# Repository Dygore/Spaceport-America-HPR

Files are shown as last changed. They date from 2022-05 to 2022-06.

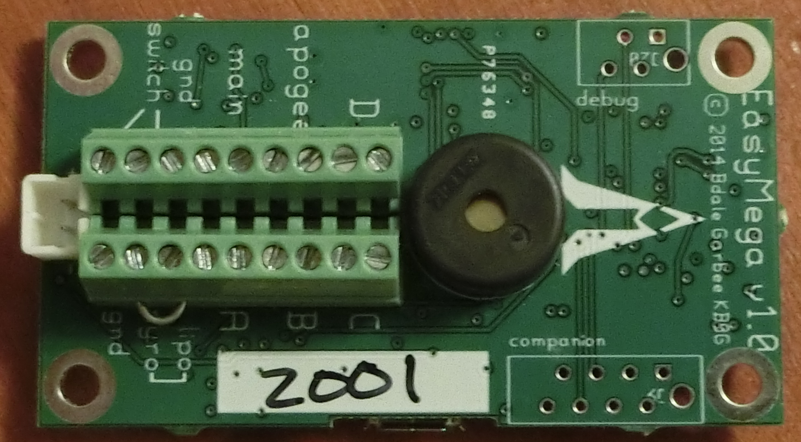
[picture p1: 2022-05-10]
altos/doc/easymega-v1.0-top.jpg

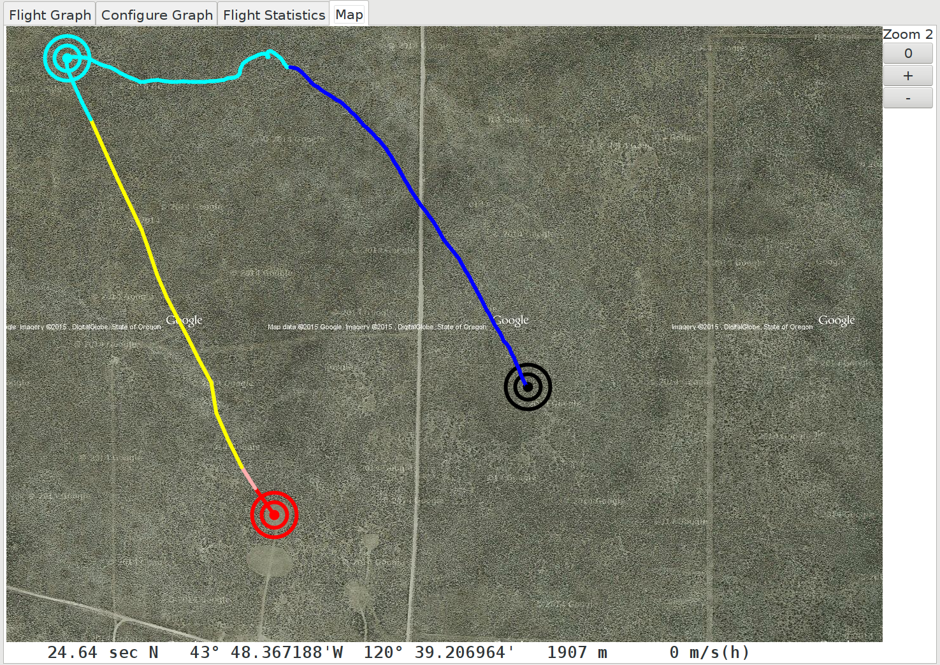
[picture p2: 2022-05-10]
altos/doc/graph-map.png

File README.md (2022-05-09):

# Oklahoma State University High Powered Rocketry Spaceport America



## About
This project will be used to create a working airbrake system for the Spaceport America Competition in June. The goal of this competition is to get as close to 10,000 feet as possible with a High Powered Rocket.

Our airbrake will be controlled by stepper motors with a gear increase for torque, which will turn a lead screw after the rocket motor has burnt out until apogee. The STM32 Board will receive telemetry data over SPI from the Telemega, it will access a lookup table on our flash chip to get the corresponding drag coefficients. It will then drive the stepper motor using a stepper motor controller to step the airbrake pads out, thus slowing down the rocket. This could be further enhanced using more accurate data and a PID controller.

## Details
The code will be written in two main sections
Section 1: STM32 code written in STM32 CubeIDE programmed using SWD pins
Section 2: Code written and built in Linux using Altus Metrum's Telemega code as a base

## References
For more information on the Altus Metrum Telemega visit https://altusmetrum.org/

Thank you to Bdale Garbee for his help in the development process and for designing the Telemega https://gag.com/bdale/

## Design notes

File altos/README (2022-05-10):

	AltOS - 8051 operating system for Altus-Metrum projects

Copyright and License

	Copyright © 2009 Keith Packard <keithp@keithp.com>

	This program is free software; you can redistribute it and/or modify
	it under the terms of the GNU General Public License as published by
	the Free Software Foundation; either version 2 of the License, or
	(at your option) any later version.

	This program is distributed in the hope that it will be useful, but
	WITHOUT ANY WARRANTY; without even the implied warranty of
	MERCHANTABILITY or FITNESS FOR A PARTICULAR PURPOSE.  See the GNU
	General Public License for more details.

	You should have received a copy of the GNU General Public License along
	with this program; if not, write to the Free Software Foundation, Inc.,
	59 Temple Place, Suite 330, Boston, MA 02111-1307 USA.

Tasking API:

	 * Multi-tasking
	 * Non-preemptive
	 * Unix-style sleep/wakeup scheduling
	 * Strict round-robin, no priorities

	uint8_t ao_sleep(void *wchan)

		Puts current task to sleep. Will wake up when wchan is
		signalled (returning 0), or when an alarm has expired
		(returning 1).
	
	void ao_wakeup(void *wchan)

		Wakeup all tasks sleeping on wchan

	void ao_add_task(struct ao_task *task, void (*start)(void))

		Adds a task to the queue of available tasks

	void ao_start_scheduler(void)

		Invokes the scheduler, starting the operating system

	void ao_yield(void)

		Switches to another task which is ready to run. Allows
		tasks which want to run for a while to give up the CPU
		without needing to sleep

	void ao_panic(uint8_t reason)

		Any fatal error should call this function, which can
		display the error code in some cryptic fashion.

	void ao_wake_task(struct ao_task *task)

		Wake the task as if the wchan it is waiting on had
		been signalled.

	void ao_alarm(uint16_t delay)

		Queue an alarm to expire 'delay' ticks in the future.
		The alarm will cause the task to wake from ao_sleep
		and return 1. Alarms are cancelled if the task is
		awoken by ao_wakeup or ao_wake_task.

	void ao_exit(void)

		Stop the current task and remove it from the list of
		available tasks.

Timer API

	 * Regular timer ticks (at 100Hz, by default)
	 * All time values are in ticks

	 uint16_t ao_time(void)

		Returns the curent tick count

	void ao_delay(uint16_t delay)

		Suspend task execution for 'delay' ticks.

DMA API

	 * Static DMA entry allocation

	uint8_t ao_dma_alloc(uint8_t *done)

		Allocates one of the 5 DMA units on the cc1111
		processor. When this DMA unit is finished, it will
		set *done to 1 and wakeup anyone waiting on that.

	void ao_dma_set_transfer(uint8_t id, void *src, void *dst,
				 uint16_t count, uint8_t cfg0, uint8_t cfg1)

		Prepares the specified DMA unit for operation.

	void ao_dma_start(uint8_t id)

		Start DMA on the specified channel.

	void ao_dma_trigger(uint8_t id)

		Manually trigger a DMA channel

	void ao_dma_abort(uint8_t id)

		Abort a pending DMA transfer, signalling
		that by setting the associated 'done' to
		AO_DMA_ABORTED and waking any task
		sleeping on that.

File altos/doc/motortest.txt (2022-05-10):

= Motor Testing: Static and In-Flight Motor Performance Testing
Bdale Garbee <bdale@gag.com>
:title-logo-image: image:../themes/background.png[]
:revnumber: v{version}
:revdate: 01 Jan 1970
:icons:
:icontype: svg
:copyright: Bdale Garbee 2021
:doctype: book
:numbered:
:stylesheet: am.css
:linkcss:
:toc:
:motortest: 1
:application: Motor Testing
:pdf-stylesdir: .
:pdf-style: altusmetrum
:pdf-fontsdir: fonts

	include::header.adoc[]

	include::motortest-intro.adoc[]

	include::motortest-configuration.adoc[]

	include::motortest-installation.adoc[]

	include::motortest-operation.adoc[]

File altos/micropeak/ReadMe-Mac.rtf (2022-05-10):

Installing MicroPeak software for Mac OS X computers

The MicroPeak distribution for Mac OS X consists of:

1) The MicroPeak application
2) Mac OS X driver for FTDI USB devices

Install the MicroPeak application by control-clicking the install-macosx script and selecting “Open” from the menu. This will display a dialog asking if you are sure you want to open it. Select “Open” from the dialog to execute the script. This will install the software, documentation and firmware in your home Applications/AltOS folder. You can move it afterwards if you choose.

To communicate with the MicroPeak serial adapter, you need to installed the FTDI device drivers, which is done by double-clicking on the FTDIUSBSerialDriver disk image. Inside that is the FTDI USB Serial Driver package. Double click on that and it will guide you through the installation process.

Thanks for choosing AltusMetrum products!

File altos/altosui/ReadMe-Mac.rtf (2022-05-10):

Installing AltOS software for Mac OS X Computers

The AltOS distribution for Mac OS X consists of:

1) The AltosUI application
2) Current AltOS firmware for Altus Metrum products

Install the AltosUI application by control-clicking the install-macosx script and selecting “Open” from the menu. This will display a dialog asking if you are sure you want to open it. Select “Open” from the dialog to execute the script. This will install the software, documentation and firmware in your home Applications/AltOS folder. You can move it afterwards if you choose.

Thanks for choosing AltusMetrum products!

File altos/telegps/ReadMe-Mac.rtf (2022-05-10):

Installing TeleGPS software for Mac OS X computers

The TeleGPS distribution for Mac OS X consists of:

1) The TeleGPS application
2) Current AltOS firmware for TeleGPS products

Install the TeleGPS application by control-clicking the install-macosx script and selecting “Open” from the menu. This will display a dialog asking if you are sure you want to open it. Select “Open” from the dialog to execute the script. This will install the software, documentation and firmware in your home Applications/AltOS folder. You can move it afterwards if you choose.

Thanks for choosing AltusMetrum products!

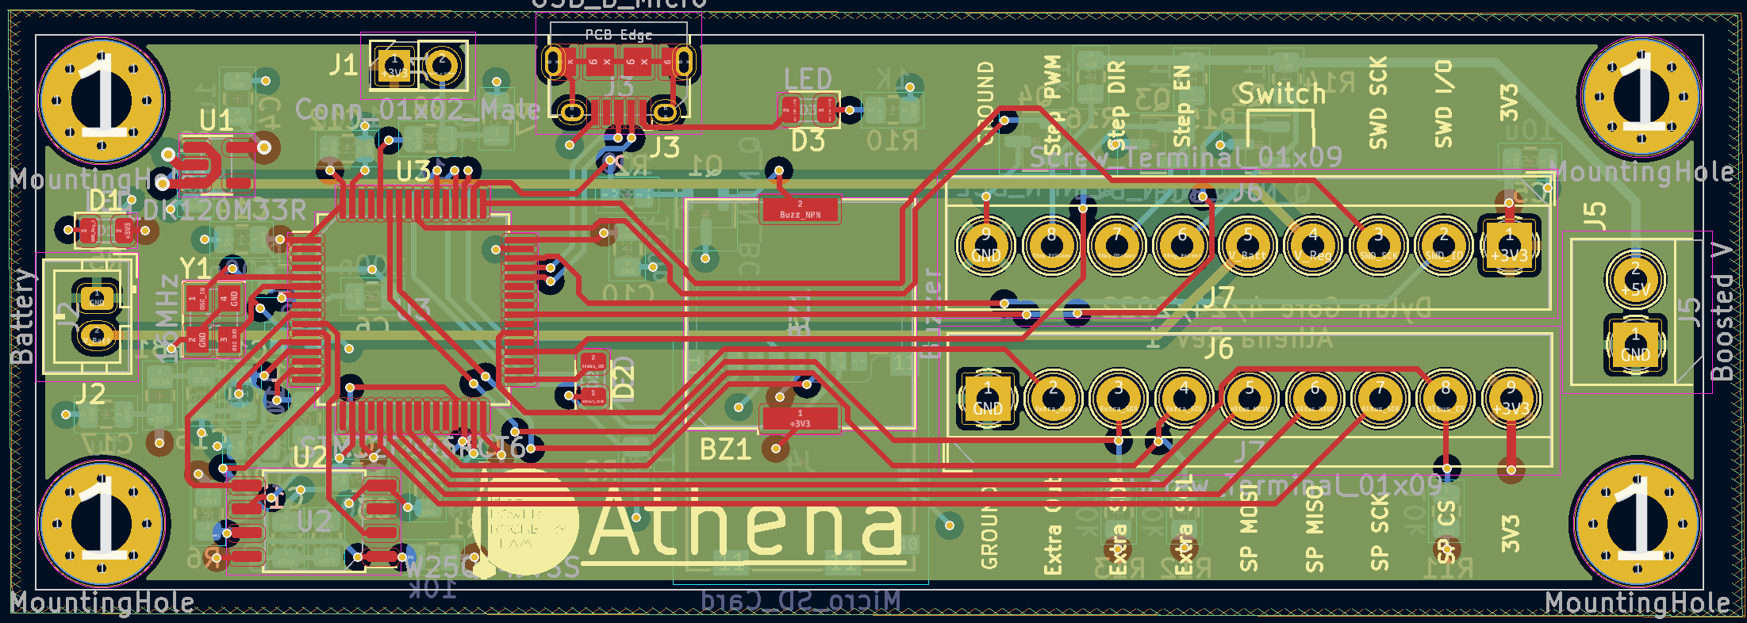
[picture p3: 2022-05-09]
Athena/PCB Overview.PNG

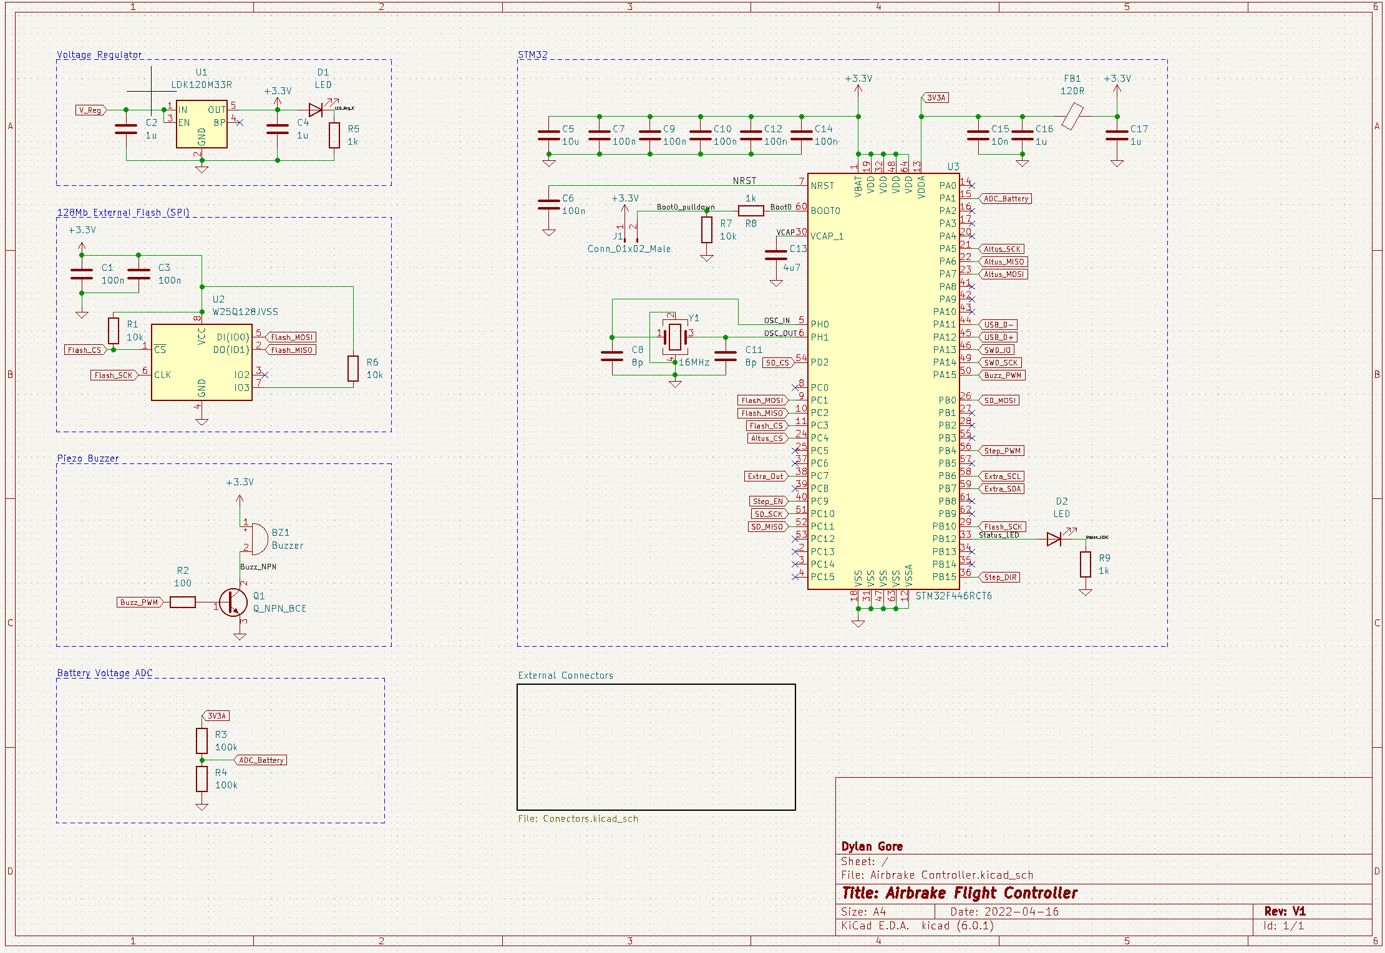
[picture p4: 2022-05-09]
Athena/Schematic 1.PNG

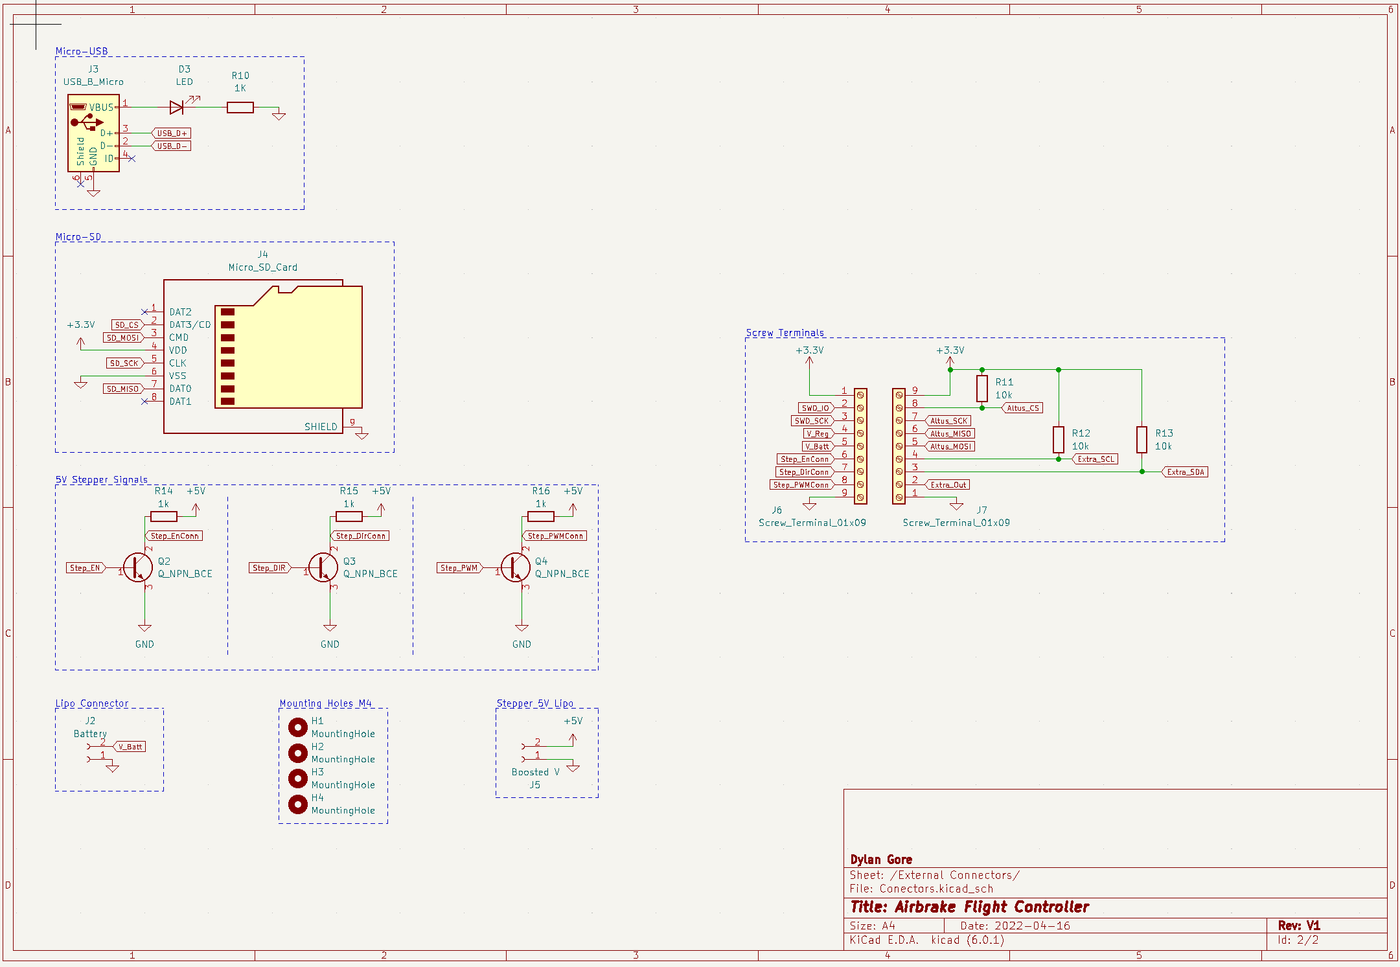
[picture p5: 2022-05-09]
Athena/Schematic 2.PNG

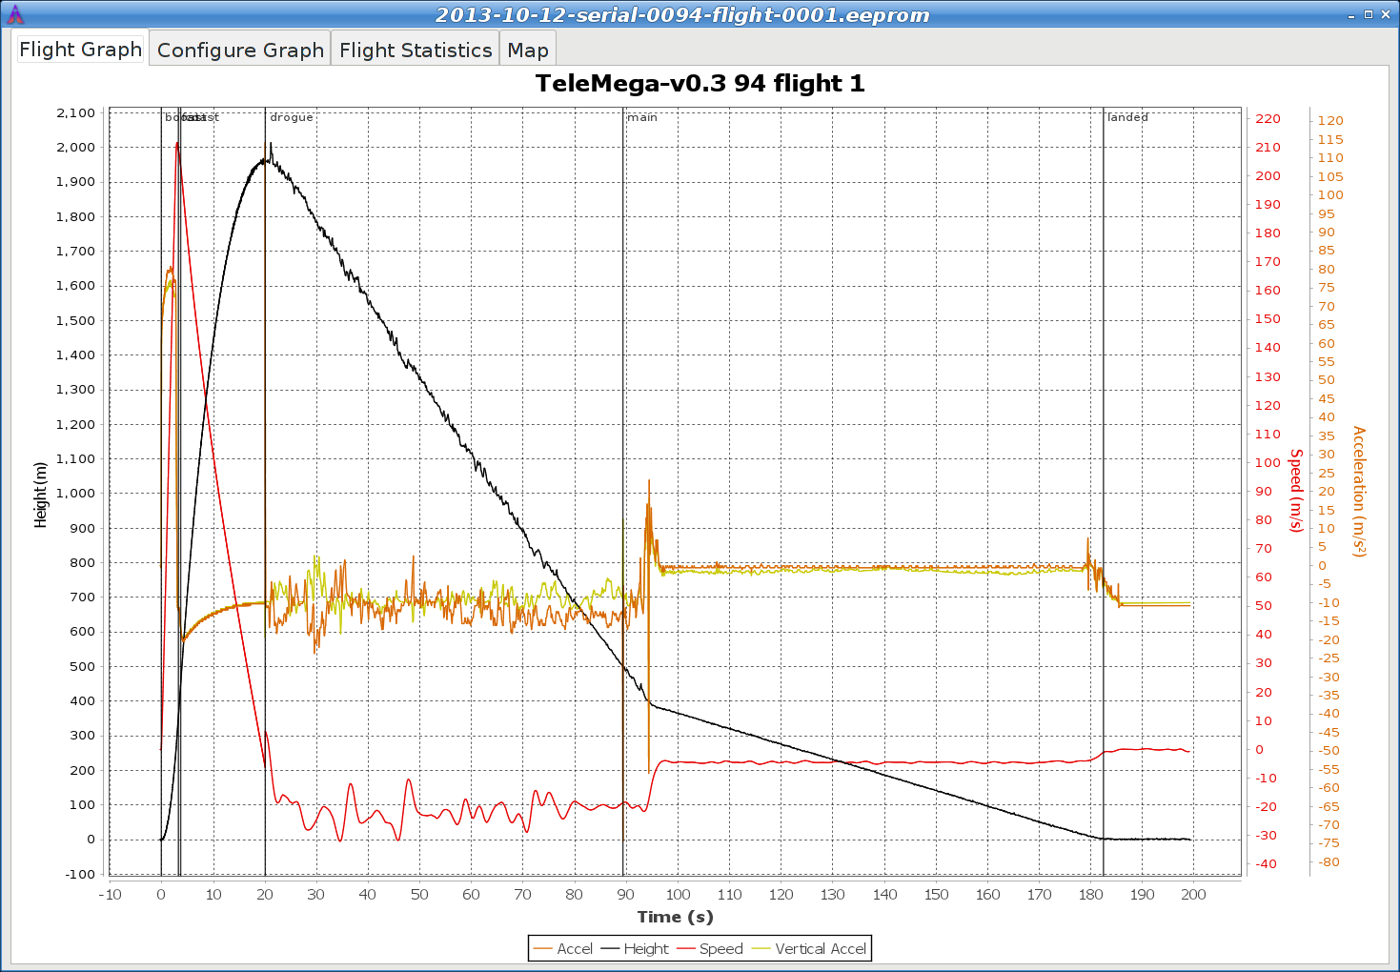
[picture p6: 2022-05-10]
altos/doc/graph.png

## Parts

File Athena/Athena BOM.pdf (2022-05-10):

Item Name | QTY Per board | Price | Part Number | Link | Total Price
Voltage Regulator | 1 | | $0.91 LDK120M33R | https://www.digikey.com/en/products/detail/stmicroelectronics/LDK120M33R/3820949 | $0.91
Cap 1uF | 4 | $0.07 CL21B105KAFNNNG https://www.digikey.com/en/products/detail/samsung-electro-mechanics/CL21B105KAFNNNG/3894465 | $0.28
Orange LED | 3 | | $0.16 LO R976-PS-1 | https://www.digikey.com/en/products/detail/osram-opto-semiconductors-inc/LO-R976-PS-1/1227955 | $0.48
1K Resistor | 6 | | $0.07 RNCP0805FTD1K00 | https://www.digikey.com/en/products/detail/stackpole-electronics-inc/RNCP0805FTD1K00/2240229 | $0.44
Cap 0.1uF | 8 | | $0.07 08055C104KAT4A | https://www.digikey.com/en/products/detail/kyocera-avx/08055C104KAT4A/6816312 | $0.58
10K Resistor | 6 | | $0.03 RMCF0805FG10K0 | https://www.digikey.com/en/products/detail/stackpole-electronics-inc/RMCF0805FG10K0/1712623 | $0.16
W25Q128 | 1 | | $1.95 W25Q128JVSIM TR | https://www.digikey.com/en/products/detail/winbond-electronics/W25Q128JVSIM-TR/6819722 | $1.95
Piezo | 1 | | $1.34 SMTB-1240-S-R | https://www.digikey.com/en/products/detail/pui-audio-inc/SMTB-1240-S-R/13165906 | $1.34
100 Resistor | 1 | | $0.10 RMCF0805FT100R | https://www.digikey.com/en/products/detail/stackpole-electronics-inc/RMCF0805FT100R/1760711 | $0.10
PNP | 4 | | $0.74 ZXTP19060CFFTA | https://www.digikey.com/en/products/detail/diodes-incorporated/ZXTP19060CFFTA/1557749 | $2.96
100K Resistor | 2 | | $0.10 RMCF0805FT100K | https://www.digikey.com/en/products/detail/stackpole-electronics-inc/RMCF0805FT100K/1760712 | $0.20
Cap 10u | 1 | | $0.22 CL21A106KAFN3NE | https://www.digikey.com/en/products/detail/samsung-electro-mechanics/CL21A106KAFN3NE/3888548 | $0.22
Cap 10n | 1 | $0.10 CL21B103KAANNNC https://www.digikey.com/en/products/detail/samsung-electro-mechanics/CL21B103KAANNNC/3888092 | $0.10
Ferrite 120 | 1 | | $0.10 ILBB0805ER121V | https://www.digikey.com/en/products/detail/vishay-dale/ILBB0805ER121V/2574906 | $0.10
Cap 4u7 | 1 | $0.13 CL21A475KQFNNNG https://www.digikey.com/en/products/detail/samsung-electro-mechanics/CL21A475KQFNNNG/3894444 | $0.13
Cap 8pf | 2 | | $0.24 08051A8R0DAT2A | https://www.digikey.com/en/products/detail/kyocera-avx/08051A8R0DAT2A/1601261 | $0.48
Sd Card Conn | 1 | $2.12 | 1040310811 https://www.digikey.com/en/products/detail/molex/1040310811/2370379 | $2.12
Screw Term 9 | 2 | $3.44 | 393570009 https://www.digikey.com/en/products/detail/molex/0393570009/1280716 | $6.88
Screw Term 2 | 1 | $0.55 | 1984617 https://www.digikey.com/en/products/detail/phoenix-contact/1984617/950849 | $0.55
Battery Connector | 1 | $0.65 2-pin JST-PH Connector (2.0 mm Pitch) https://www.solarbotics.com/product/hvjst2 | $0.65
USB Micro | 1 | | $0.48 10118194-0001LF | https://www.digikey.com/en/products/detail/amphenol-icc-fci/10118194-0001LF/2785389 | $0.48
STM32 | 1 | | $18.65 C915971 | https://jlcpcb.com/parts/componentSearch?isSearch=true&searchTxt=crystal%20oscillator | $18.65 Assembled by JLC, not from DigiKey
Osc | 1 | | $0.90 C13738 | https://jlcpcb.com/parts/componentSearch?isSearch=true&searchTxt=crystal%20oscillator | $0.90 Assembled by JLC, not from DigiKey
Total | 51 | | | | $40.67

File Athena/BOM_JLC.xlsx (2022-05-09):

Comment | Designator | Footprint | JLCPCB Part #（optional）
STM32 | U3 | Package_QFP:LQFP-64_10x10mm_P0.5mm | C915971
Crystal Oscillator | Y1 | Crystal:Crystal_SMD_3225-4Pin_3.2x2.5mm | C13738

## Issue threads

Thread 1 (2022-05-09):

Integrate Flash Chip

Dygore, 2022-05-09:

Dygore, 2022-05-09:
Read/Write array's to the flash chip using STM32 HAL SPI library

Dygore, 2022-06-02:
Chip ID has been read in, implemented write enable/disable.
Still Needed: Chip clear in sections and read/write array and regular data.
Implement data check in startup and display it over COMM

Dygore, 2022-06-07:
Flash Chip Integrated

Closed 2022-06-07.

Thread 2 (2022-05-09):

Stepper Motor Controller Integration

Dygore, 2022-05-09:

Dygore, 2022-05-09:
Controller Stepper motor with 5V rail and PWM. PNP transistors Logic is backwards!

Dygore, 2022-05-10:
Code Implemented, can be tested after board soldering and motor test stand creation

Dygore, 2022-05-16:
Test needed on Athena, worked on previous board

Closed 2022-06-01.

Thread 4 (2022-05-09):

SPI Slave

Dygore, 2022-05-09:

Dygore, 2022-05-09:
Receive data from Telemega over SPI get device id at beginning to indicate beginning of transmission

Dygore, 2022-05-16:
Read to get beginning transmission, in startup function. Once received send back connection transmission and go into low power mode state.

Dygore, 2022-06-13:
Scrapping low power mode, handshake works, integrate into startup then go into waiting for state change state

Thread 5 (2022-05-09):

SPI Master

Dygore, 2022-05-09:

Dygore, 2022-05-09:
Transmit data over SPI to slave device use device id as beginning to indicate beginning of transmission

Dygore, 2022-05-16:
Send until reads back connection data, then wait until state change

Dygore, 2022-06-13:
Handshake works, start sending data once handshake has been completed

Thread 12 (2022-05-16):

Startup

Dygore, 2022-05-16:

Dygore, 2022-05-16:
Buzzer, test motor and buzzer at the end have been implemented

Dygore, 2022-05-16:
All systems working!

Closed 2022-05-16.

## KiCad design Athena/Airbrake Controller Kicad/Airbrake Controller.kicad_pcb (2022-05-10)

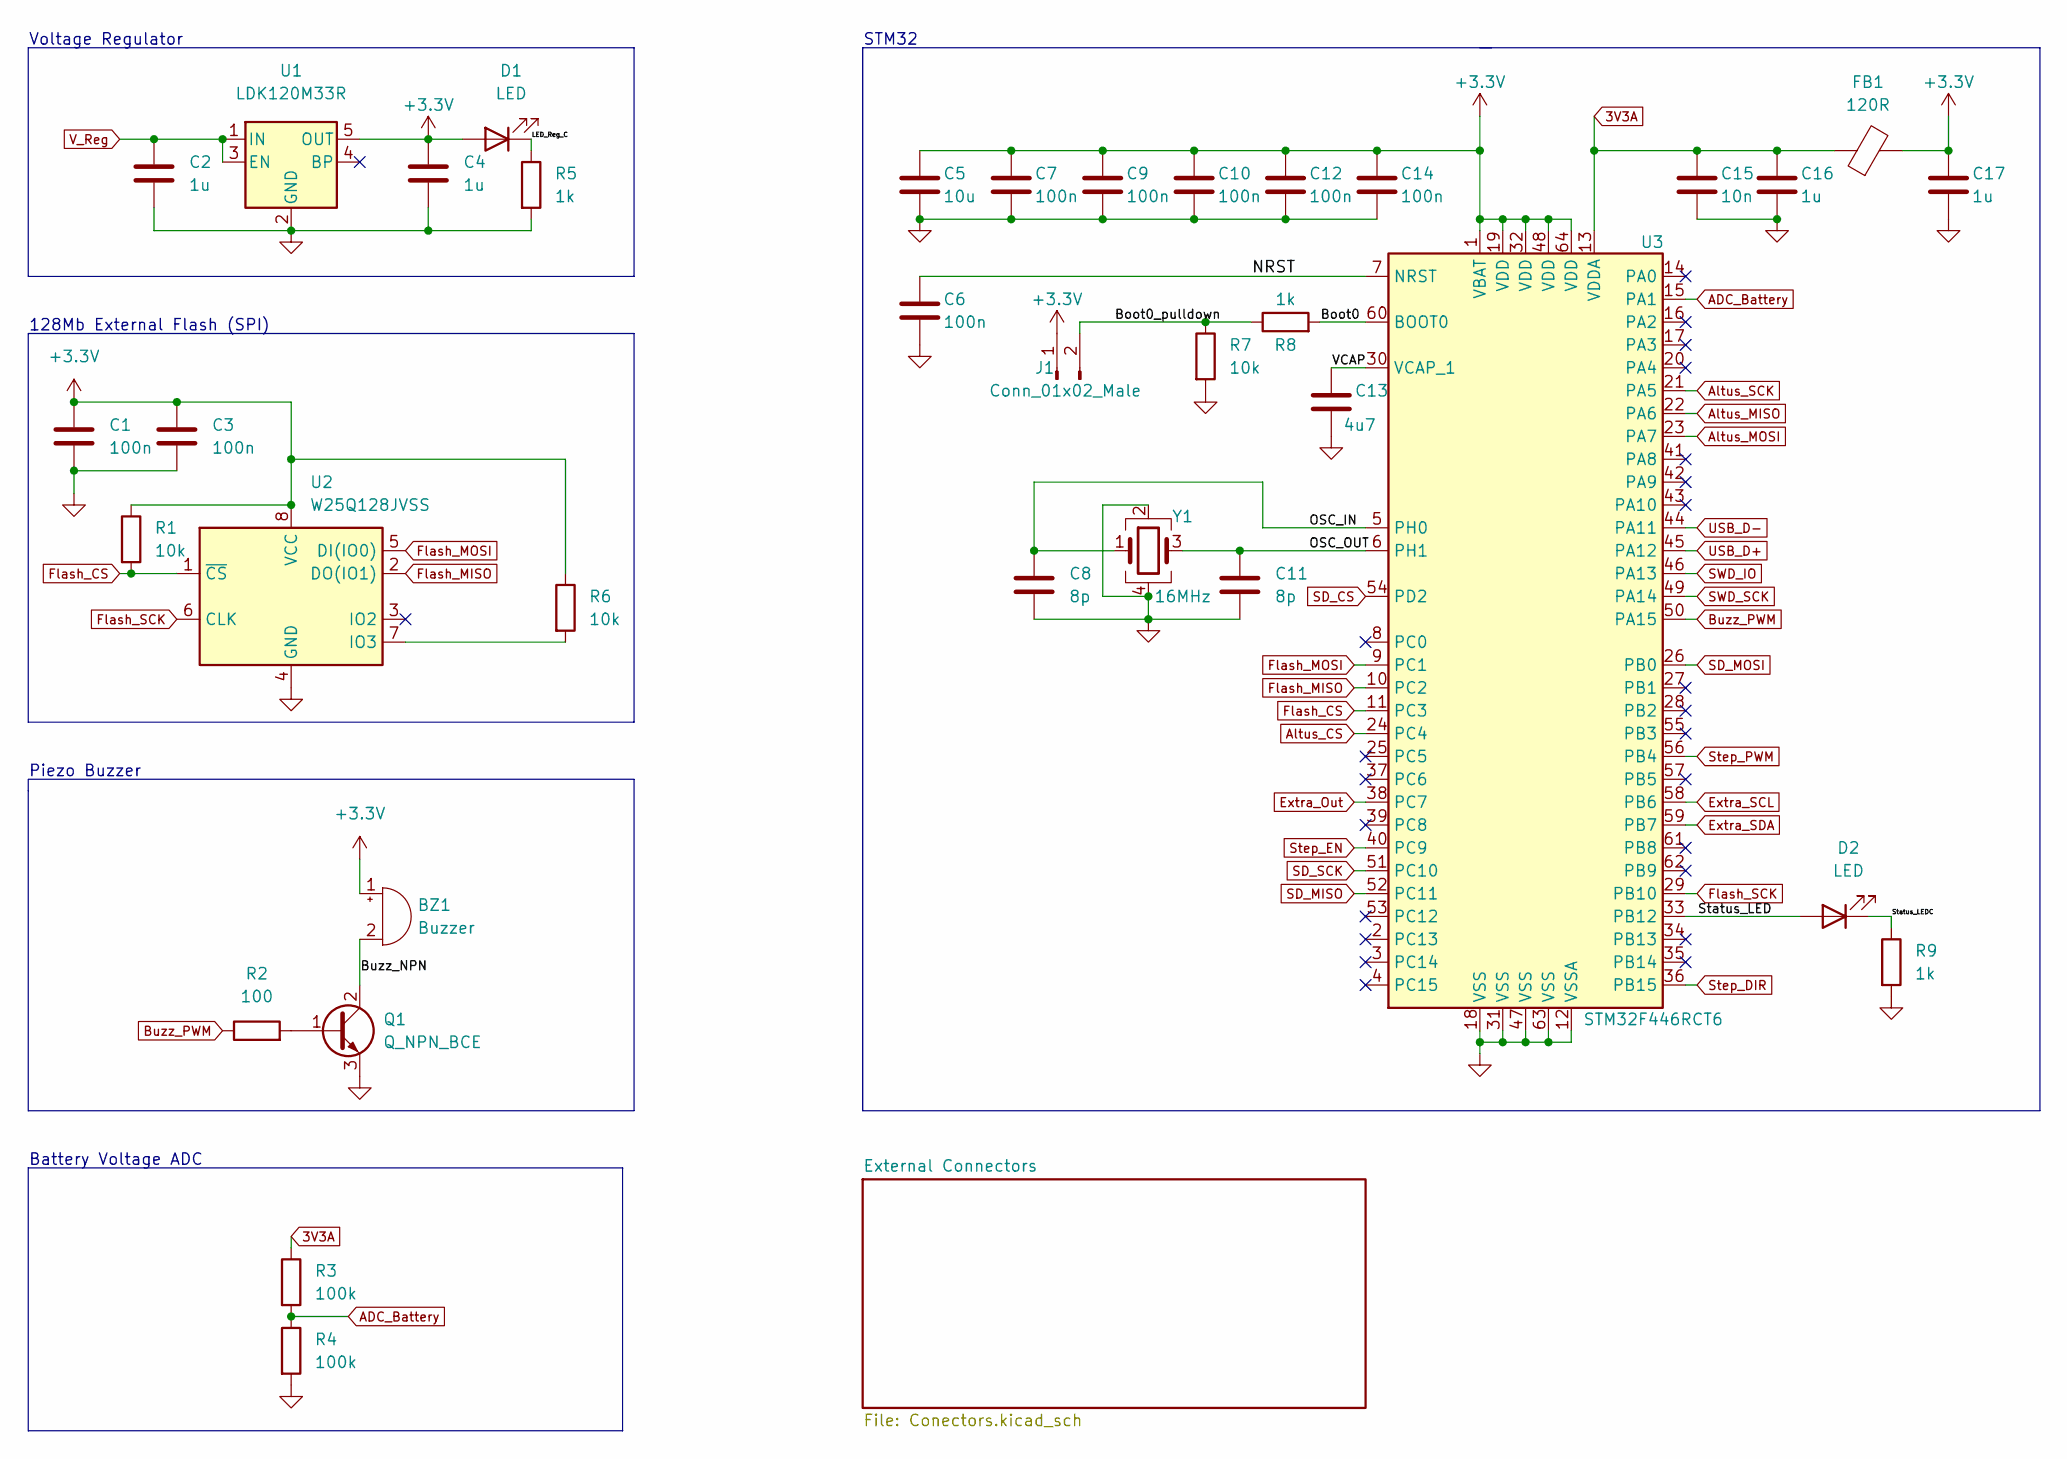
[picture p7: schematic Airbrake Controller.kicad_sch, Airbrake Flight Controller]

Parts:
BZ1: Buzzer; Buzzer_Murata_PKLCS1212E
C1, C3, C6, C7, C9, C10, C12, C14: 100n; C_0805_2012Metric
C2, C4, C16, C17: 1u; C_0805_2012Metric
C5: 10u; C_0805_2012Metric
C8, C11: 8p; C_0805_2012Metric
C13: 4u7; C_0805_2012Metric
C15: 10n; C_0805_2012Metric
D1, D2: LED; LED_0805_2012Metric
FB1: 120R; R_0805_2012Metric_Pad1.20x1.40mm_HandSolder
J1: Conn_01x02_Male; PinHeader_2x01_P2.54mm_Vertical
Q1: Q_NPN_BCE; SOT-23
R1, R6, R7: 10k; R_0805_2012Metric
R2: 100; R_0805_2012Metric
R3, R4: 100k; R_0805_2012Metric
R5, R8, R9: 1k; R_0805_2012Metric
U1: LDK120M33R; SOT-23-5
U2: W25Q128JVSS; SOIC-8_5.23x5.23mm_P1.27mm
U3: STM32F446RCT6; LQFP-64_10x10mm_P0.5mm
Y1: 16MHz; Crystal_SMD_3225-4Pin_3.2x2.5mm

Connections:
3V3A: C15.1, C16.1, FB1.1, R3.1, U3.13 (VDDA)
+3V3: BZ1.1 (-), C1.1, C3.1, C4.1, C5.1, C7.1, C9.1, C10.1, C12.1, C14.1, C17.1, D1.2 (A), FB1.2, J1.1, R1.1, R6.1, U1.5 (OUT), U2.8 (VCC), U3.1 (VBAT), U3.19 (VDD), U3.32 (VDD), U3.48 (VDD), U3.64 (VDD); also elsewhere on the board
/Boot0: R8.2, U3.60 (BOOT0)
/Boot0_pulldown: J1.2, R7.1, R8.1
/Buzz_NPN: BZ1.2 (+), Q1.2 (C)
/LED_Reg_C: D1.1 (K), R5.1
/NRST: C6.1, U3.7 (NRST)
/OSC_IN: C8.1, U3.5 (PH0), Y1.1
/OSC_OUT: C11.1, U3.6 (PH1), Y1.3
/Status_LED: D2.2 (A), U3.33 (PB12)
/Status_LEDC: D2.1 (K), R9.1
/VCAP: C13.1, U3.30 (VCAP_1)
ADC_Battery: R3.2, R4.1, U3.15 (PA1)
Altus_CS: U3.24 (PC4); also elsewhere on the board
Altus_MISO: U3.22 (PA6); also elsewhere on the board
Altus_MOSI: U3.23 (PA7); also elsewhere on the board
Altus_SCK: U3.21 (PA5); also elsewhere on the board
Buzz_PWM: R2.1, U3.50 (PA15)
Extra_Out: U3.38 (PC7); also elsewhere on the board
Extra_SCL: U3.58 (PB6); also elsewhere on the board
Extra_SDA: U3.59 (PB7); also elsewhere on the board
Flash_CS: R1.2, U2.1 (~CS), U3.11 (PC3)
Flash_MISO: U2.2 (DO(IO1)), U3.10 (PC2)
Flash_MOSI: U2.5 (DI(IO0)), U3.9 (PC1)
Flash_SCK: U2.6 (CLK), U3.29 (PB10)
GND: C1.2, C2.2, C3.2, C4.2, C5.2, C6.2, C7.2, C8.2, C9.2, C10.2, C11.2, C12.2, C13.2, C14.2, C15.2, C16.2, C17.2, Q1.3 (E), R4.2, R5.2, R7.2, R9.2, U1.2 (GND), U2.4 (GND), U3.12 (VSSA), U3.18 (VSS), U3.31 (VSS), U3.47 (VSS), U3.63 (VSS), Y1.2, Y1.4; also elsewhere on the board
unnamed: Q1.1 (B), R2.2
unnamed: R6.2, U2.7 (IO3)
SD_CS: U3.54 (PD2); also elsewhere on the board
SD_MISO: U3.52 (PC11); also elsewhere on the board
SD_MOSI: U3.26 (PB0); also elsewhere on the board
SD_SCK: U3.51 (PC10); also elsewhere on the board
SWD_IO: U3.46 (PA13); also elsewhere on the board
SWD_SCK: U3.49 (PA14); also elsewhere on the board
Step_DIR: U3.36 (PB15); also elsewhere on the board
Step_EN: U3.40 (PC9); also elsewhere on the board
Step_PWM: U3.56 (PB4); also elsewhere on the board
USB_D+: U3.45 (PA12); also elsewhere on the board
USB_D-: U3.44 (PA11); also elsewhere on the board
V_Reg: C2.1, U1.1 (IN), U1.3 (EN); also elsewhere on the board

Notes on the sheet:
Voltage Regulator
128Mb External Flash (SPI)
Piezo Buzzer
Battery Voltage ADC
STM32

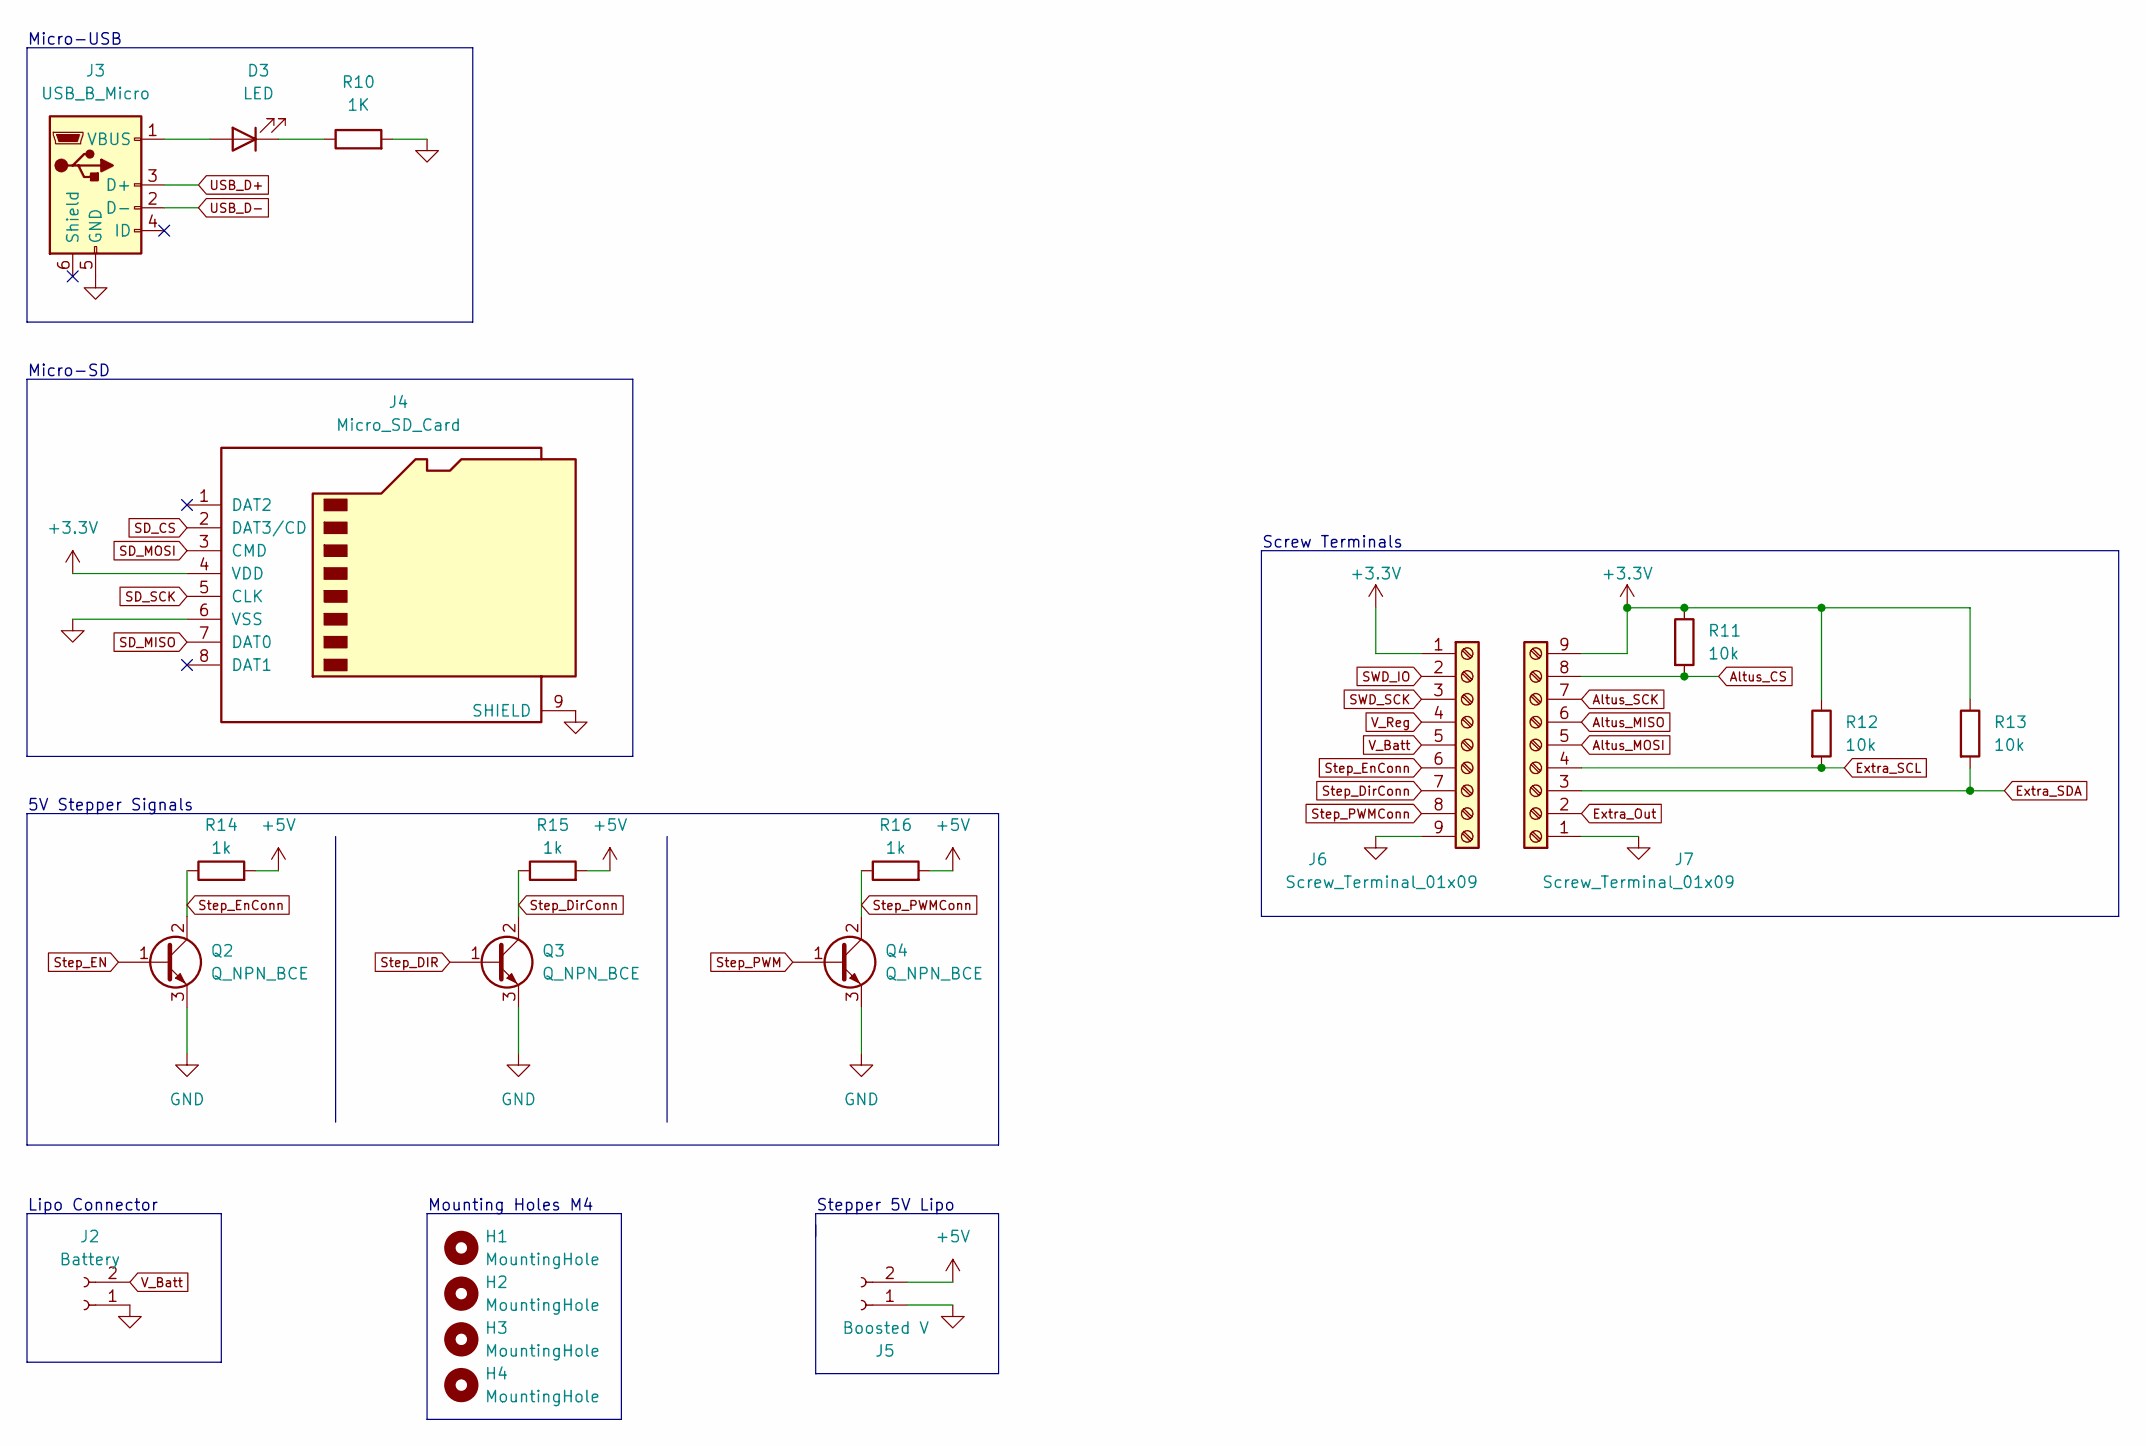
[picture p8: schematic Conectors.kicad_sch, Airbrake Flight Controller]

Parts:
D3: LED; LED_0805_2012Metric
H1, H2, H4: MountingHole; MountingHole_3.2mm_M3_Pad_Via
H3: MountingHole; MountingHole_3mm_Pad_Via
J2: Battery; JST_PH_B2B-PH-K_1x02_P2.00mm_Vertical
J3: USB_B_Micro; USB_Micro-B_Amphenol_10118194_Horizontal
J4: Micro_SD_Card; microSD_HC_Molex_104031-0811
J5: Boosted V; TerminalBlock_4Ucon_1x02_P3.50mm_Horizontal
J6, J7: Screw_Terminal_01x09; TerminalBlock_4Ucon_1x09_P3.50mm_Horizontal
Q2, Q3, Q4: Q_NPN_BCE; SOT-23
R10: 1K; R_0805_2012Metric
R11, R12, R13: 10k; R_0805_2012Metric
R14, R15, R16: 1k; R_0805_2012Metric

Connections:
+3V3: J4.4 (VDD), J6.1, J7.9, R11.1, R12.1, R13.1; also elsewhere on the board
+5V: J5.2, R14.2, R15.2, R16.2
Altus_CS: J7.8, R11.2; also elsewhere on the board
Altus_MISO: J7.6; also elsewhere on the board
Altus_MOSI: J7.5; also elsewhere on the board
Altus_SCK: J7.7; also elsewhere on the board
Extra_Out: J7.2; also elsewhere on the board
Extra_SCL: J7.4, R12.2; also elsewhere on the board
Extra_SDA: J7.3, R13.2; also elsewhere on the board
GND: J2.1, J3.5 (GND), J4.6 (VSS), J4.9 (SHIELD), J5.1, J6.9, J7.1, Q2.3 (E), Q3.3 (E), Q4.3 (E), R10.2; also elsewhere on the board
unnamed: D3.1 (K), R10.1
unnamed: D3.2 (A), J3.1 (VBUS)
SD_CS: J4.2 (DAT3/CD); also elsewhere on the board
SD_MISO: J4.7 (DAT0); also elsewhere on the board
SD_MOSI: J4.3 (CMD); also elsewhere on the board
SD_SCK: J4.5 (CLK); also elsewhere on the board
SWD_IO: J6.2; also elsewhere on the board
SWD_SCK: J6.3; also elsewhere on the board
Step_DIR: Q3.1 (B); also elsewhere on the board
Step_DirConn: J6.7, Q3.2 (C), R15.1
Step_EN: Q2.1 (B); also elsewhere on the board
Step_EnConn: J6.6, Q2.2 (C), R14.1
Step_PWM: Q4.1 (B); also elsewhere on the board
Step_PWMConn: J6.8, Q4.2 (C), R16.1
USB_D+: J3.3 (D+); also elsewhere on the board
USB_D-: J3.2 (D-); also elsewhere on the board
V_Batt: J2.2, J6.5
V_Reg: J6.4; also elsewhere on the board

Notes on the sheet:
Micro-USB
5V Stepper Signals
Lipo Connector
Stepper 5V Lipo
Screw Terminals
Micro-SD
Mounting Holes M4

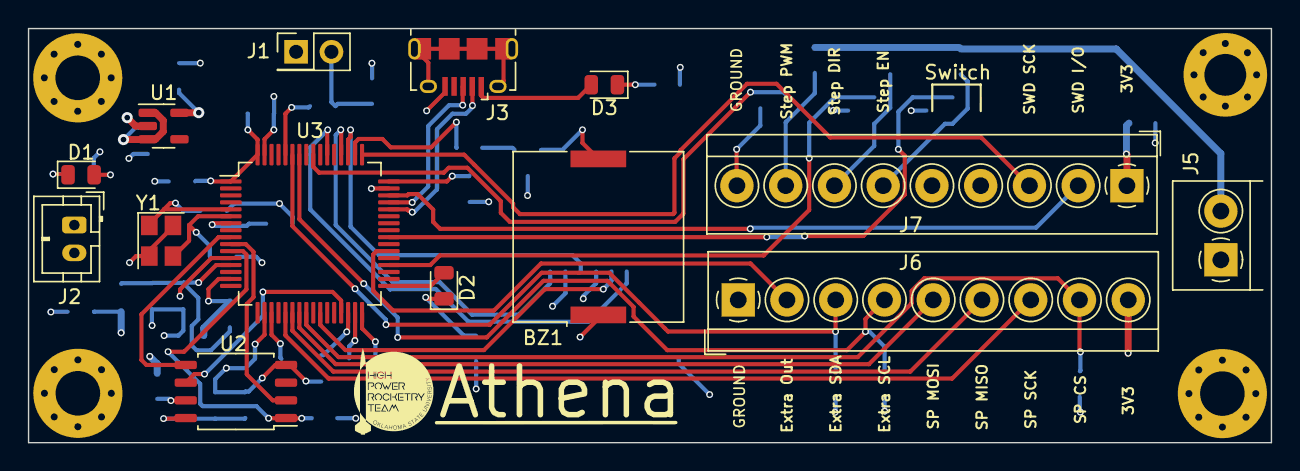
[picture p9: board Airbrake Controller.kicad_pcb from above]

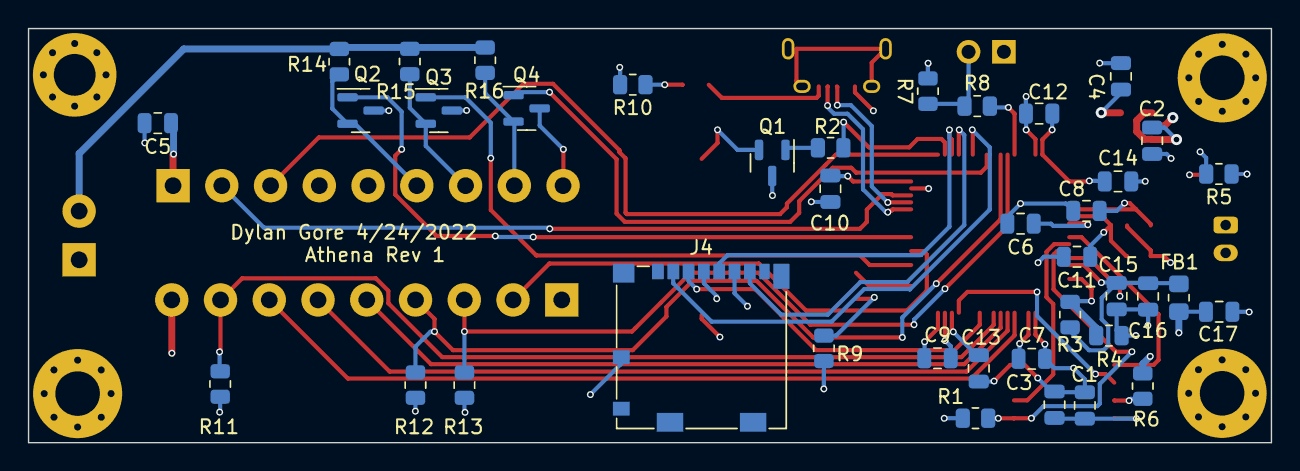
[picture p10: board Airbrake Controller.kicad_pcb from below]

Board: 4 copper layers, 89.2 x 29.7 mm, 57 parts (39 on the bottom side), 47 nets.

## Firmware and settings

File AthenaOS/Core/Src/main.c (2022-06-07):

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
/* Includes ------------------------------------------------------------------*/
#include "main.h"
#include "usb_device.h"

/* USER CODE BEGIN Includes */

#include "Stepper.h"
#include "Status_LED.h"
#include "flash.h"

#include "usbd_cdc_if.h"

#include "string.h"

#include <stdio.h>


/* USER CODE END Includes */

/* USER CODE BEGIN PD */
double VBatt = 0;
/* USER CODE END PD */

 ADC_HandleTypeDef hadc1;

I2C_HandleTypeDef hi2c1;

SPI_HandleTypeDef hspi1;
SPI_HandleTypeDef hspi2;
SPI_HandleTypeDef hspi3;

TIM_HandleTypeDef htim2;

void SystemClock_Config(void);
static void MX_GPIO_Init(void);
static void MX_ADC1_Init(void);
static void MX_I2C1_Init(void);
static void MX_SPI1_Init(void);
static void MX_SPI2_Init(void);
static void MX_SPI3_Init(void);
static void MX_TIM2_Init(void);
/* USER CODE BEGIN PFP */
void startup(void);
void buzz(int freq, int duration);
/* USER CODE END PFP */

/**
  * @brief  The application entry point.
  * @retval int
  */
int main(void)
{
  /* USER CODE BEGIN 1 */


	HAL_GPIO_WritePin(GPIOB, Step_PWM_Pin, GPIO_PIN_SET);
	HAL_GPIO_WritePin(GPIOC, Step_EN_Pin, GPIO_PIN_SET);

  /* USER CODE END 1 */

  /* MCU Configuration--------------------------------------------------------*/

  /* Reset of all peripherals, Initializes the Flash interface and the Systick. */
  HAL_Init();

  /* Configure the system clock */
  SystemClock_Config();

  /* Initialize all configured peripherals */
  MX_GPIO_Init();
  MX_ADC1_Init();
  MX_I2C1_Init();
  MX_SPI1_Init();
  MX_SPI2_Init();
  MX_SPI3_Init();
  MX_TIM2_Init();
  MX_USB_DEVICE_Init();
  /* Infinite loop */
  /* USER CODE BEGIN WHILE */

  HAL_TIM_Base_Start(&htim2);

  startup();

  uint8_t grid[5] = {0x00, 0x01, 0x02, 0x03, 0x04};

  flashWriteArray(0x00, 0x00, 0x00, grid, 4);

  HAL_Delay(50);

  char txBuff[105];

  while (1)
  {
    /* USER CODE END WHILE */

    /* USER CODE BEGIN 3 */

	 sprintf(txBuff, "Read Data Addr1: %X, Read Data Addr2: %X, Read Data Addr3: %X, Read Data Addr4: %X, Read Data Addr5: %X\n", flashRead(0x00, 0x00, 0x00), flashRead(0x00, 0x00, 0x01), flashRead(0x00, 0x00, 0x02), flashRead(0x00, 0x00, 0x03), flashRead(0x00, 0x00, 0x04));

	 status_LED_Swap();
	 HAL_Delay(100);
	 status_LED_Swap();
	 HAL_Delay(100);

	 CDC_Transmit_FS((uint8_t *)txBuff, strlen(txBuff));
  }
  /* USER CODE END 3 */
}

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
/* USER CODE BEGIN 4 */
void delay (uint16_t us)
{
  __HAL_TIM_SET_COUNTER(&htim2, 0);
  while (__HAL_TIM_GET_COUNTER(&htim2) < us);
}

void startup(void){
	double f = 256.41;
	for(int i = 0; i < 5; i++){
			for(int i = 0; i < 500; i++){
				HAL_GPIO_WritePin(Buzz_PWM_GPIO_Port, Buzz_PWM_Pin, GPIO_PIN_SET);
				delay(f*0.5);
				HAL_GPIO_WritePin(Buzz_PWM_GPIO_Port, Buzz_PWM_Pin, GPIO_PIN_RESET);
				delay(f*0.5);
			}
			HAL_Delay(100);
	}

	HAL_Delay(1000);

	HAL_ADC_Start(&hadc1);
	HAL_ADC_PollForConversion(&hadc1, HAL_MAX_DELAY);

	VBatt = (((double)HAL_ADC_GetValue(&hadc1)*2)/4095)*3.3;

	f = 250;
	for(int i = 0; i < (int)VBatt; i++){
		for(int i = 0; i < 700; i++){
			HAL_GPIO_WritePin(Buzz_PWM_GPIO_Port, Buzz_PWM_Pin, GPIO_PIN_SET);
			delay(f*0.60);
			HAL_GPIO_WritePin(Buzz_PWM_GPIO_Port, Buzz_PWM_Pin, GPIO_PIN_RESET);
			delay(f*0.40);
		}
		HAL_Delay(400);
	}

	HAL_Delay(600);

	f = 250;
	for(int i = 0; i < (int)((VBatt-(int)VBatt)*10); i++){
		for(int i = 0; i < 700; i++){
			HAL_GPIO_WritePin(Buzz_PWM_GPIO_Port, Buzz_PWM_Pin, GPIO_PIN_SET);
			delay(f*0.60);
			HAL_GPIO_WritePin(Buzz_PWM_GPIO_Port, Buzz_PWM_Pin, GPIO_PIN_RESET);
			delay(f*0.40);
		}
		HAL_Delay(400);
	}

	HAL_Delay(1000);

	f = 256.41;
	for(int i = 0; i < 500; i++){
		HAL_GPIO_WritePin(Buzz_PWM_GPIO_Port, Buzz_PWM_Pin, GPIO_PIN_SET);
		delay(f*0.60);
		HAL_GPIO_WritePin(Buzz_PWM_GPIO_Port, Buzz_PWM_Pin, GPIO_PIN_RESET);
		delay(f*0.40);
	}

	HAL_Delay(100);

	f = 250;
	for(int i = 0; i < 500; i++){
		HAL_GPIO_WritePin(Buzz_PWM_GPIO_Port, Buzz_PWM_Pin, GPIO_PIN_SET);
		delay(f*0.60);
		HAL_GPIO_WritePin(Buzz_PWM_GPIO_Port, Buzz_PWM_Pin, GPIO_PIN_RESET);
		delay(f*0.40);
	}

	HAL_Delay(100);

	f = 243.9;
	for(int i = 0; i < 500; i++){
		HAL_GPIO_WritePin(Buzz_PWM_GPIO_Port, Buzz_PWM_Pin, GPIO_PIN_SET);
		delay(f*0.60);
		HAL_GPIO_WritePin(Buzz_PWM_GPIO_Port, Buzz_PWM_Pin, GPIO_PIN_RESET);
		delay(f*0.40);
	}

	HAL_Delay(100);

	f = 238.095;
	for(int i = 0; i < 500; i++){
		HAL_GPIO_WritePin(Buzz_PWM_GPIO_Port, Buzz_PWM_Pin, GPIO_PIN_SET);
		delay(f*0.60);
		HAL_GPIO_WritePin(Buzz_PWM_GPIO_Port, Buzz_PWM_Pin, GPIO_PIN_RESET);
		delay(f*0.40);
	}

	HAL_Delay(1000);

	stepper_Step (1, 50); //Step in direction 1, 50 steps

	HAL_Delay(1000);

	stepper_Step (1, 50); //Step in direction 1, 50 steps

	HAL_Delay(1000);

	stepper_Step (0, 50); //Step in direction 0, 50 steps

	HAL_Delay(1000);

	stepper_Step (0, 50); //Step in direction 0, 50 steps

	f = 232.55814;
	for(int i = 0; i < 10000; i++){
		HAL_GPIO_WritePin(Buzz_PWM_GPIO_Port, Buzz_PWM_Pin, GPIO_PIN_SET);
		delay(f*0.60);
		HAL_GPIO_WritePin(Buzz_PWM_GPIO_Port, Buzz_PWM_Pin, GPIO_PIN_RESET);
		delay(f*0.40);
	}

	HAL_Delay(100);
}

uint8_t W25Q_Spi(uint8_t Data)
{
	uint8_t ret;
	HAL_SPI_TransmitReceive(&hspi2, &Data, &ret, 1, HAL_MAX_DELAY);
	return ret;
}

/* USER CODE END 4 */
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


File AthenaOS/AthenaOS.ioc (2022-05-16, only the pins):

Mcu.UserName=STM32F446RCTx
PA1.GPIO_Label=ADC_Batt
PA1.Signal=ADCx_IN1
PA11.GPIO_Label=USB-
PA11.Signal=USB_OTG_FS_DM
PA12.GPIO_Label=USB+
PA12.Signal=USB_OTG_FS_DP
PA13.Signal=SYS_JTMS-SWDIO
PA14.Signal=SYS_JTCK-SWCLK
PA15.GPIO_Label=Buzz_PWM
PA15.Signal=GPIO_Output
PA5.GPIO_Label=Altus_SCK
PA5.Signal=SPI1_SCK
PA6.GPIO_Label=Altus_MISO
PA6.Signal=SPI1_MISO
PA7.GPIO_Label=Altus_MOSI
PA7.Signal=SPI1_MOSI
PB0.GPIO_Label=SD_MOSI
PB0.Signal=SPI3_MOSI
PB10.GPIO_Label=Flash_SCK
PB10.Signal=SPI2_SCK
PB12.GPIO_Label=Status_LED
PB12.Signal=GPIO_Output
PB15.GPIO_Label=Step_DIR
PB15.Signal=GPIO_Output
PB4.GPIO_Label=Step_PWM
PB4.Signal=GPIO_Output
PB6.GPIO_Label=Extra_SCL
PB6.Signal=I2C1_SCL
PB7.GPIO_Label=Extra_SDA
PB7.Signal=I2C1_SDA
PC1.GPIO_Label=Flash_MOSI
PC1.Signal=SPI2_MOSI
PC10.GPIO_Label=SD_SCK
PC10.Signal=SPI3_SCK
PC11.GPIO_Label=SD_MISO
PC11.Signal=SPI3_MISO
PC2.GPIO_Label=Flash_MISO
PC2.Signal=SPI2_MISO
PC3.GPIO_Label=Flash_CS
PC3.Signal=GPIO_Output
PC4.GPIO_Label=Altus_CS
PC4.Signal=GPIO_Input
PC7.GPIO_Label=Extra_out
PC7.Signal=GPIO_Output
PC9.GPIO_Label=Step_EN
PC9.Signal=GPIO_Output
PD2.GPIO_Label=SD_CS
PD2.Signal=GPIO_Output
PH0-OSC_IN.Signal=RCC_OSC_IN
PH1-OSC_OUT.Signal=RCC_OSC_OUT

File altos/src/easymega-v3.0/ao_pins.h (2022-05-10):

/*
 * Copyright © 2014 Bdale Garbee <bdale@gag.com>
 *
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
 * You should have received a copy of the GNU General Public License along
 * with this program; if not, write to the Free Software Foundation, Inc.,
 * 59 Temple Place, Suite 330, Boston, MA 02111-1307 USA.
 */

#ifndef _AO_PINS_H_
#define _AO_PINS_H_


/* 16MHz High speed external crystal */
#define AO_HSE			16000000

/* PLLVCO = 96MHz (so that USB will work) */
#define AO_PLLMUL		6
#define AO_RCC_CFGR_PLLMUL	(STM_RCC_CFGR_PLLMUL_6)

/* SYSCLK = 32MHz (no need to go faster than CPU) */
#define AO_PLLDIV		3
#define AO_RCC_CFGR_PLLDIV	(STM_RCC_CFGR_PLLDIV_3)

/* HCLK = 32MHz (CPU clock) */
#define AO_AHB_PRESCALER	1
#define AO_RCC_CFGR_HPRE_DIV	STM_RCC_CFGR_HPRE_DIV_1

/* Run APB1 at 16MHz (HCLK/2) */
#define AO_APB1_PRESCALER	2
#define AO_RCC_CFGR_PPRE1_DIV	STM_RCC_CFGR_PPRE2_DIV_2

/* Run APB2 at 16MHz (HCLK/2) */
#define AO_APB2_PRESCALER	2
#define AO_RCC_CFGR_PPRE2_DIV	STM_RCC_CFGR_PPRE2_DIV_2

#define HAS_SERIAL_1		0
#define USE_SERIAL_1_STDIN	0
#define SERIAL_1_PB6_PB7	0
#define SERIAL_1_PA9_PA10	0

#define HAS_SERIAL_2		0
#define USE_SERIAL_2_STDIN	0
#define SERIAL_2_PA2_PA3	0
#define SERIAL_2_PD5_PD6	0

#define HAS_SERIAL_3		0
#define USE_SERIAL_3_STDIN	0
#define SERIAL_3_PB10_PB11	0
#define SERIAL_3_PC10_PC11	0
#define SERIAL_3_PD8_PD9	0

#define ao_gps_getchar		ao_serial1_getchar
#define ao_gps_putchar		ao_serial1_putchar
#define ao_gps_set_speed	ao_serial1_set_speed
#define ao_gps_fifo		(ao_stm_usart1.rx_fifo)

#define AO_CONFIG_DEFAULT_FLIGHT_LOG_MAX	(1024 * 1024)
#define AO_CONFIG_MAX_SIZE                     1024
#define LOG_ERASE_MARK                         0x55
#define LOG_MAX_ERASE                          128
#define AO_LOG_FORMAT				AO_LOG_FORMAT_EASYMEGA_2

#define HAS_EEPROM		1
#define USE_INTERNAL_FLASH	0
#define USE_EEPROM_CONFIG	1
#define USE_STORAGE_CONFIG	0
#define HAS_USB			1
#define HAS_BEEP		1
#define BEEPER_TIMER		2
#define BEEPER_CHANNEL		3
#define BEEPER_PORT		(&stm_gpioa)
#define BEEPER_PIN		2
#define HAS_BATTERY_REPORT	1
#define HAS_RADIO		0
#define HAS_TELEMETRY		0
#define HAS_APRS		0
#define HAS_COMPANION		1

#define HAS_SPI_1		1
#define SPI_1_PA5_PA6_PA7	1	/* Barometer */
#define SPI_1_PB3_PB4_PB5	1	/* Accelerometer */
#define SPI_1_PE13_PE14_PE15	0
#define SPI_1_OSPEEDR		STM_OSPEEDR_10MHz

#define HAS_SPI_2		1
#define SPI_2_PB13_PB14_PB15	1	/* Flash, IMU, Companion */
#define SPI_2_PD1_PD3_PD4	0
#define SPI_2_OSPEEDR		STM_OSPEEDR_10MHz

#define HAS_I2C_1		1
#define I2C_1_PB8_PB9		1

#define HAS_I2C_2		0
#define I2C_2_PB10_PB11		0

#define PACKET_HAS_SLAVE	0
#define PACKET_HAS_MASTER	0

#define LOW_LEVEL_DEBUG		0

#define LED_PORT_ENABLE		STM_RCC_AHBENR_GPIOAEN
#define LED_PORT		(&stm_gpioa)
#define LED_PIN_RED		9
#define LED_PIN_GREEN		10
#define AO_LED_RED		(1 << LED_PIN_RED)
#define AO_LED_GREEN		(1 << LED_PIN_GREEN)

#define LEDS_AVAILABLE		(AO_LED_RED | AO_LED_GREEN)

#define HAS_GPS			0
#define HAS_FLIGHT		1
#define HAS_ADC			1
#define HAS_ADC_TEMP		1
#define HAS_LOG			1

/*
 * Igniter
 */

#define HAS_IGNITE		1
#define HAS_IGNITE_REPORT	1

#define AO_SENSE_PYRO(p,n)	((p)->adc.sense[n])
#define AO_SENSE_DROGUE(p)	((p)->adc.sense[4])
#define AO_SENSE_MAIN(p)	((p)->adc.sense[5])
#define AO_IGNITER_CLOSED	400
#define AO_IGNITER_OPEN		60

/* Pyro A */
#define AO_PYRO_PORT_0	(&stm_gpioa)
#define AO_PYRO_PIN_0	15

/* Pyro B */
#define AO_PYRO_PORT_1	(&stm_gpioc)
#define AO_PYRO_PIN_1	10

/* Pyro C */
#define AO_PYRO_PORT_2	(&stm_gpiob)
#define AO_PYRO_PIN_2	11

/* Pyro D */
#define AO_PYRO_PORT_3	(&stm_gpiob)
#define AO_PYRO_PIN_3	10

/* Drogue */
#define AO_IGNITER_DROGUE_PORT	(&stm_gpioa)
#define AO_IGNITER_DROGUE_PIN	0

/* Main */
#define AO_IGNITER_MAIN_PORT	(&stm_gpioa)
#define AO_IGNITER_MAIN_PIN	1

/* Number of general purpose pyro channels available */
#define AO_PYRO_NUM	4

/*
 * ADC
 */
#define AO_DATA_RING		32
#define AO_ADC_NUM_SENSE	6

struct ao_adc {
	int16_t			sense[AO_ADC_NUM_SENSE];
	int16_t			v_batt;
	int16_t			v_pbatt;
	int16_t			temp;
};

#define AO_ADC_DUMP(p) \
	printf("tick: %5u A: %5d B: %5d C: %5d D: %5d drogue: %5d main: %5d batt: %5d pbatt: %5d temp: %5d\n", \
	       (p)->tick, \
	       (p)->adc.sense[0], (p)->adc.sense[1], (p)->adc.sense[2], \
	       (p)->adc.sense[3], (p)->adc.sense[4], (p)->adc.sense[5], \
	       (p)->adc.v_batt, (p)->adc.v_pbatt, (p)->adc.temp)

#define AO_ADC_SENSE_A		14
#define AO_ADC_SENSE_A_PORT	(&stm_gpioc)
#define AO_ADC_SENSE_A_PIN	4

#define AO_ADC_SENSE_B		15
#define AO_ADC_SENSE_B_PORT	(&stm_gpioc)
#define AO_ADC_SENSE_B_PIN	5

#define AO_ADC_SENSE_C		13
#define AO_ADC_SENSE_C_PORT	(&stm_gpioc)
#define AO_ADC_SENSE_C_PIN	3

#define AO_ADC_SENSE_D		12
#define AO_ADC_SENSE_D_PORT	(&stm_gpioc)
#define AO_ADC_SENSE_D_PIN	2

#define AO_ADC_SENSE_DROGUE	11
#define AO_ADC_SENSE_DROGUE_PORT	(&stm_gpioc)
#define AO_ADC_SENSE_DROGUE_PIN	1

#define AO_ADC_SENSE_MAIN	10
#define AO_ADC_SENSE_MAIN_PORT	(&stm_gpioc)
#define AO_ADC_SENSE_MAIN_PIN	0
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

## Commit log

2022-05-10 Change File Name
    [Airbrake Controller-3V3_Cu.gbr, Airbrake Controller-B_Cu.gbr, Airbrake Controller-B_Mask.gbr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]
2022-05-10 Move BOM
2022-05-10 AthenaOS: Stepper/Status LED
2022-06-07 Flash Chip Driver

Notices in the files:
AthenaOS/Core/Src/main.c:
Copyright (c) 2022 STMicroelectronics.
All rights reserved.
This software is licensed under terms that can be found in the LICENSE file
